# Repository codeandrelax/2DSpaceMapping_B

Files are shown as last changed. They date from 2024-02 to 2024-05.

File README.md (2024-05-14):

# AUTONOMNO VOZILO - PROJEKTNI ZADATAK
Ovaj repozitorijum sadži dokumentaciju potrebnu za izradu projektnog zadataka iz predmeta Računarska elektronika/Mikrokontrolerski sistemi na Elektrotehničkom fakultetu u Banjoj Luci. Na projekatu rade tri studenta na četvrtoj godini. Cilj projekta jeste implementacija sistema za autonomnu vožnju koji može bezbijedno i efikasno upravljati vozilom. Sistem se nadograđuje na [Joy-car](https://joy-it.net/en/products/mb-joy-car) sa specificiranim zahtjevima.

# Specifikacija projektnog zadataka 
### Upravljačka PCB ploča
Potrebno je realizovati PCB pločicu koja ispunjava sljedeće zahtjeve: 
* PCB pločica može biti maksimalno dvoslojna.
* Koristi se SMD tip komponenti
* Minimalna širina veze prilikom rutiranja iznosi 0.254 mm, a minimalno rastojanje između komponenata 0.1 mm.
* Korišćenje mikrokontrolera (MCU) tipa PIC24FJ64GAxx za upravljanje i kontrolu sistema.
* Podrška za komunikaciju putem UART, SPI i I2C interfejsa za povezivanje različitih komponenti.
* Integracija Wi-Fi modula za bežičnu komunikaciju i daljinsko upravljanje.
* Upotreba već postojećeg baterijskog napajanja.
* Budzet za kupovinu komponenata od 20 do 30 dolara.

### IR Distance Click senzor
* Kretanje vozila na osnovu očitavanja senzora
* Implementacija 2D mapiranja prostora oko vozila na osnovu očivatanja senzora.

## Aplikacija
* Razvoj aplikacije za prikazivanje okoline oko vozila.
* Mogućnost pokretanja i zaustavljanja vozila putem aplikacije, 2D prikaz reljefa.
   
## Projektovanje štampane ploče
* Šema 
kompletna_sema

* Layout  
  
  back_cu
  

* 3D model
  3d_model
 3d_model2

## Realizacija algoritma kretanja vozila

Potpuno integrisano samoupravljajuće vozilo Joy Car funkcioniše na taj način da se IR click senzor vozila najprije centrira tako da skenira prostor ispred sebe i vozilo se počinje kretati ravno, to je jedan od pet mogućih pravaca kretanja vozila. Nakon što vozilo prilikom kretanja naiđe na prepreku koja se nalazi na udaljenosti od 15cm, zaustavlja se i skenira se prostor oko vozila, tako što se okreće IR Distance Click senzor koji je postavljen na servo motoru koji se okreće za ugao od 45 stepeni u desnu stranu, odnosno lijevu. Nakon što na osnovu vrijednosti napona koju senzor generiše odredimo u kojem smjeru se prepreka nalazi najdalje, vozilo se počinje kretati u tom pravcu. Ukoliko su vrijednosti očitavanja senzora veće, tada se prepreka nalazi bliže vozilu i obratno. U slučaju da se prepreka nalazi jako blizu tada autić zbog širine točkova nije u mogućnosti da nesmetano skrene u željenom pravcu pa postoji i dodatni smijer kretanja, unazad. Tada autić najprije vozi nekoliko centimetara unazad, a zatim skrene u pravcu za koji je utvrdio da je najpovoljniji.  

Na slici ispod je prikazan primjer simulacije kretanja autića u lavirintu. 

  
  
Na gifu ispod prikazano je kretanje autića kroz lavirint:

gif

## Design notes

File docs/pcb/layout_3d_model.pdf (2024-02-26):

Projektni zadatak iz predmeta Mikrokontrolerski sistemi/Računarska elektronika

1

### Elektrotehnički fakultet Univerzitet u Banjoj Luci

## DOKUMENTACIJA PROJEKTNOG ZADATKA

## iz predmeta

## MIKROKONTROLERSKI SISTEMI/RAČUNARSKA ELEKTRONIKA

Student: | Mentori:
Tripić, Nemanja | prof. dr Željko Ivanović
Legenović, Dajana | dipl. inž Damjan Prerad
Savković, Božana

Projektni zadatak iz predmeta Digitalna obrada signala - izvještaj

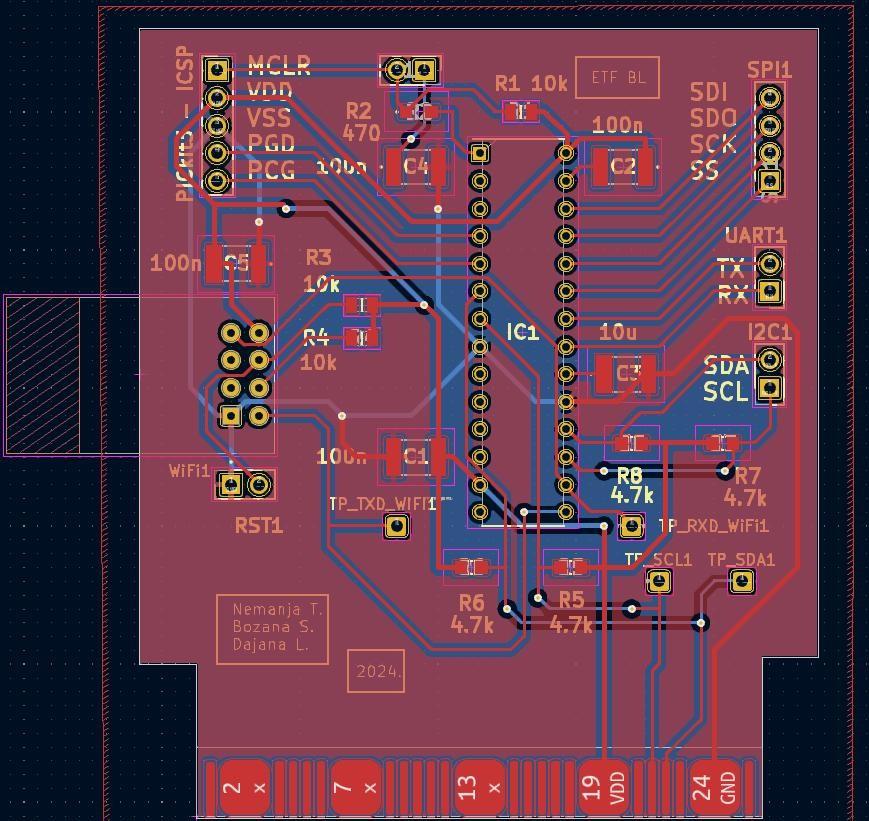
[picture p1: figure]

2

## RUTIRANJE KOMPONENATA

## Rutiranje komponenata

Nakon projektovanja šeme, potrebno je odraditi PCB layuot, rutirati komponente. Korišeno je dvoslojno rutiranje. Debljine linija za povezivanje su 0.254mm, a za napajanje 0.5mm. Minimalno rastojanje između komponenata je 0.1mm.

## Layout

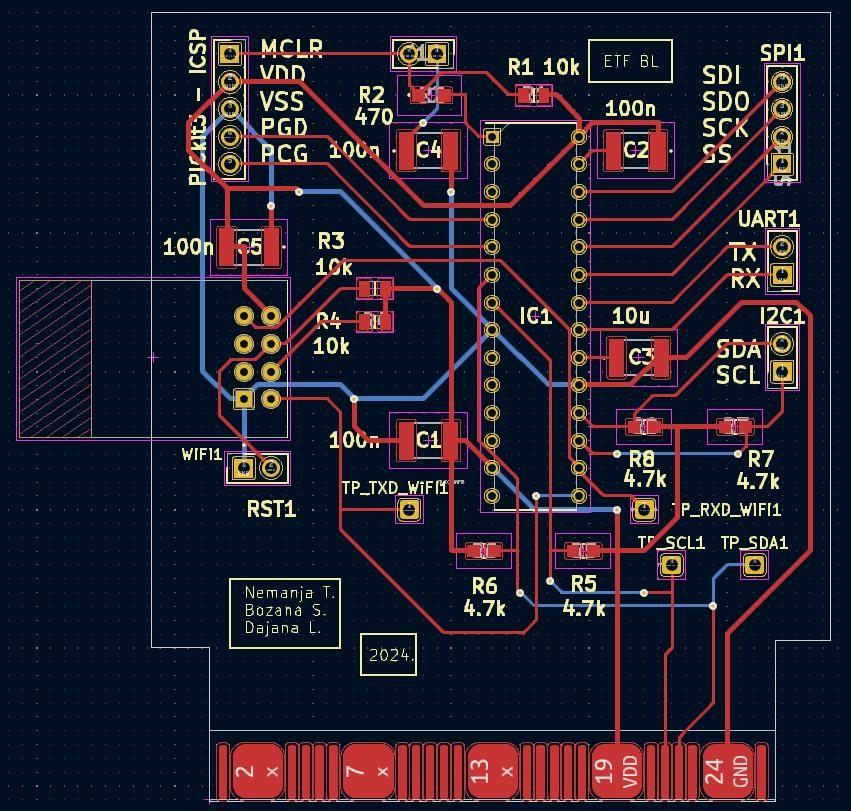
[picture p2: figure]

3

Prednja strana:

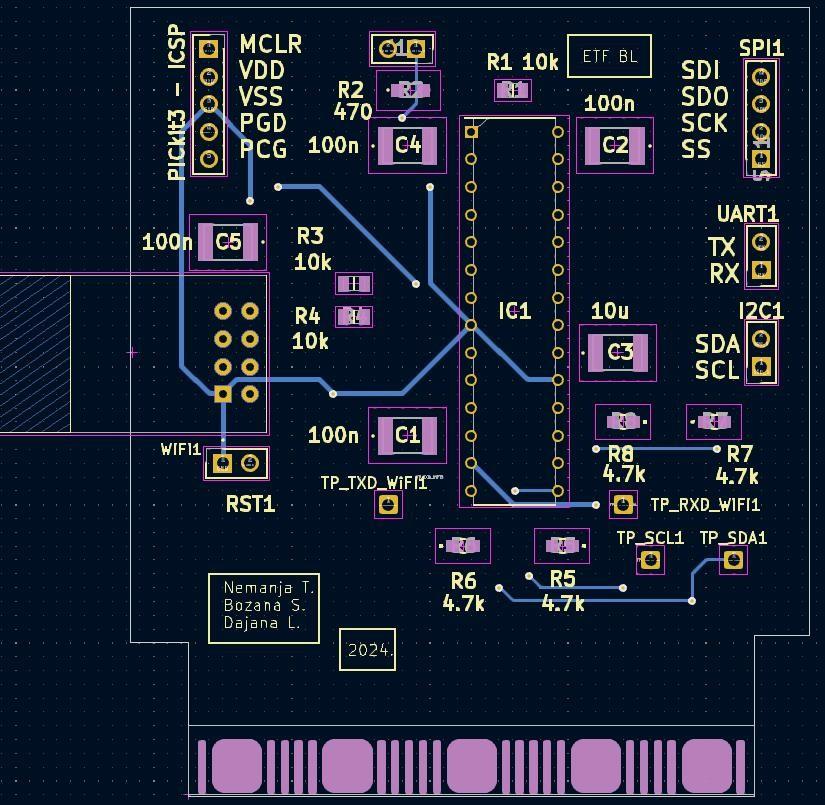
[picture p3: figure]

4

Zadnja strana:

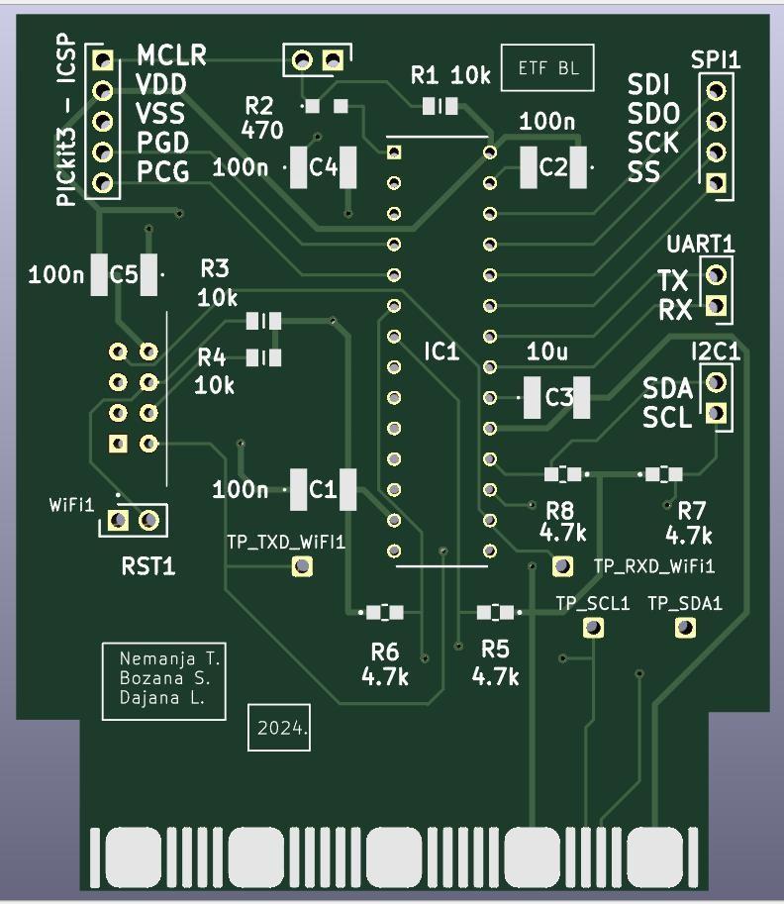
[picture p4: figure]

5

## 3D MODEL

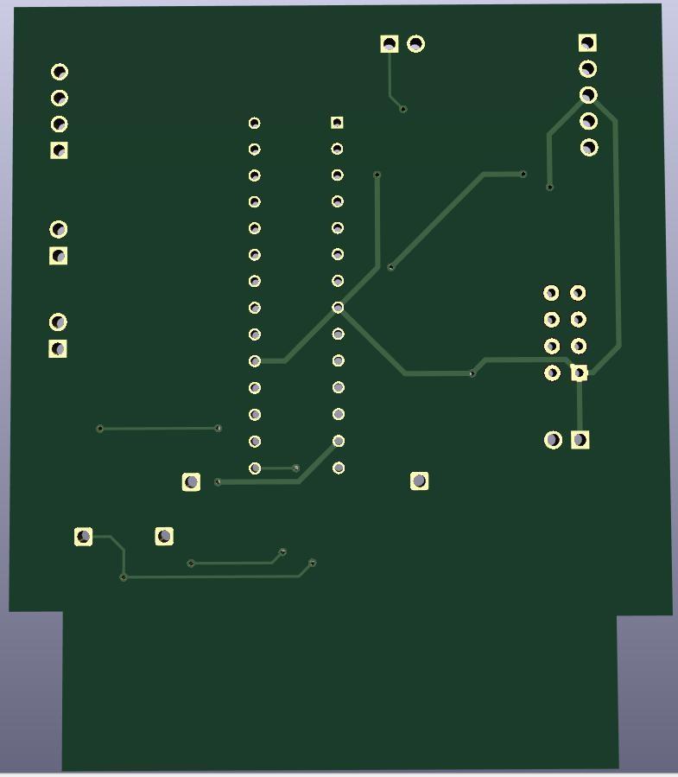
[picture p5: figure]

6

7

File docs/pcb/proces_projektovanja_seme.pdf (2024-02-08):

Projektni zadatak iz predmeta Mikrokontrolerski sistemi/Računarska elektronika

1

### Elektrotehnički fakultet Univerzitet u Banjoj Luci

## DOKUMENTACIJA PROJEKTNOG ZADATKA

## iz predmeta

## MIKROKONTROLERSKI SISTEMI/RAČUNARSKA ELEKTRONIKA

Student: | Mentori:
Tripić, Nemanja | prof. dr Željko Ivanović
Legenović, Dajana | dipl. inž Damjan Prerad
Savković, Božana

Projektni zadatak iz predmeta Digitalna obrada signala - izvještaj

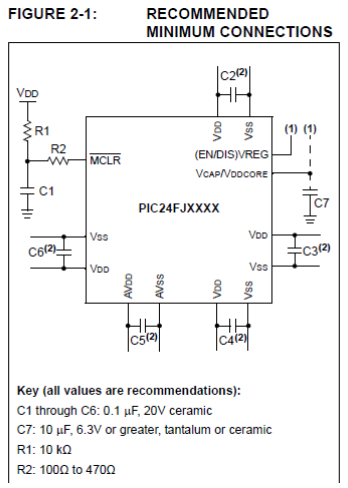
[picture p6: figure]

2

## PROJEKTOVANJE ŠEME

Kao što je već rečeno na wiki stranici stranici Planiranje projektovanja šeme, postoji nekoliko faza projektovanja. Prva faza je izbor mikrokontrolera koji zadovoljava specifikacije i dalje projektovanje ide u zavisnosti od njega. Izabran je mikrokontroler PIC24FJG4GA002 i njegov datasheet je na linku https://ww1.microchip.com/downloads/aemDocuments/documents/OTH/ProductDocuments/DataSheets/39881e.pdf. (https://ww1.microchip.com/downloads/aemDocuments/documents/OTH/ProductDocuments/DataSheets/39881e.pdf)

## 1. Dodavanje mikrokontrolera i osnovne šeme

U datasheet-u se može naći preporučena osnovna šema ukoliko se izabere dati mikrokontroler. Ona izgleda ovako:

Slika 1 – Minimalna šema

Dakle neophodno je koristiti sprežne kondenzatore između pinove VDD i VSS vrijednosti 0.1uF. Što se tiče šeme to je za sada sve što nam je bitno, ali za kasnije projektovanje biće bitno referencirati se na datasheet da bi se izabrao pravi tip kondenzatora, kao i minimalna daljina postavljanja pinova u odnosu na pinove mikrokontrolera.

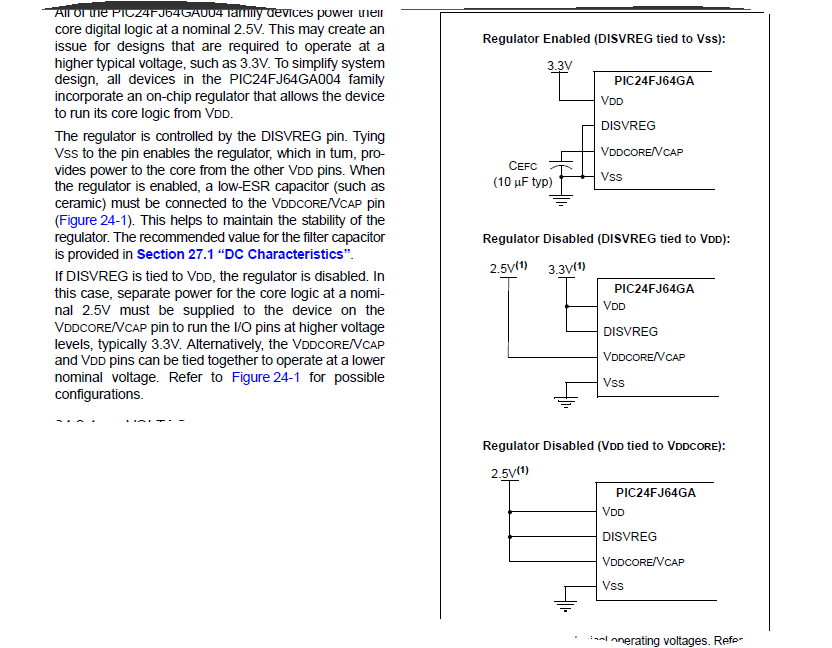
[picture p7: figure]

3

Dalje imamo dva otpornika jedan vrijednosti 10kΩ i drugi od 100Ω do 470Ω, te kondenzator od 0.1uF povezani na MCLR pin i na odgovarajući način na napajanje i na masu. MCLR pin ima dvije funkcije, koristi se pri programiranju i pri resetovanju mikrokontrolera. Detaljnije o tome kada budemo govorili o [dodavanju bloka za programiranje na šemu](#dodavanje-bloka-za-programiranje-na-šemu).

Ono što je još ostalo za kao dio osnovne konfiguracije šeme jeste spajanje pinova DISVREG (u slučaju našeg mikrokontrolera), te pina VCAP/VDDCORE. Ovi pinovi služe za omogućenje odnosno onemogućenje naponskog regulatora. Ukoliko želimo da naponski regulator bude omogućen potrebno je DISVREG spojiti na GND, a u tom slučaju VCAP/VDDCORE se spaja preko low-ESR(<5Ω) keramičkog kondenzatora od 10uF na GND.

Ako želimo da onemogućimo regulator spajamo DISVREG na VDD, a u tom slučaju je na VCAP/VDDCORE potrebno dovesti posebno napajanje sa nominalnih 2.5V. Opciono u ovom slučaju, moguće je i DISVREG i VCAP/VDDCORE spojiti na isti nominalni napon od 2.5V. Vidi datasheet (strana 215).

Slika ispod:

Slika 2 – Šema spajanja DISVREG i VCAP/VDDCORE

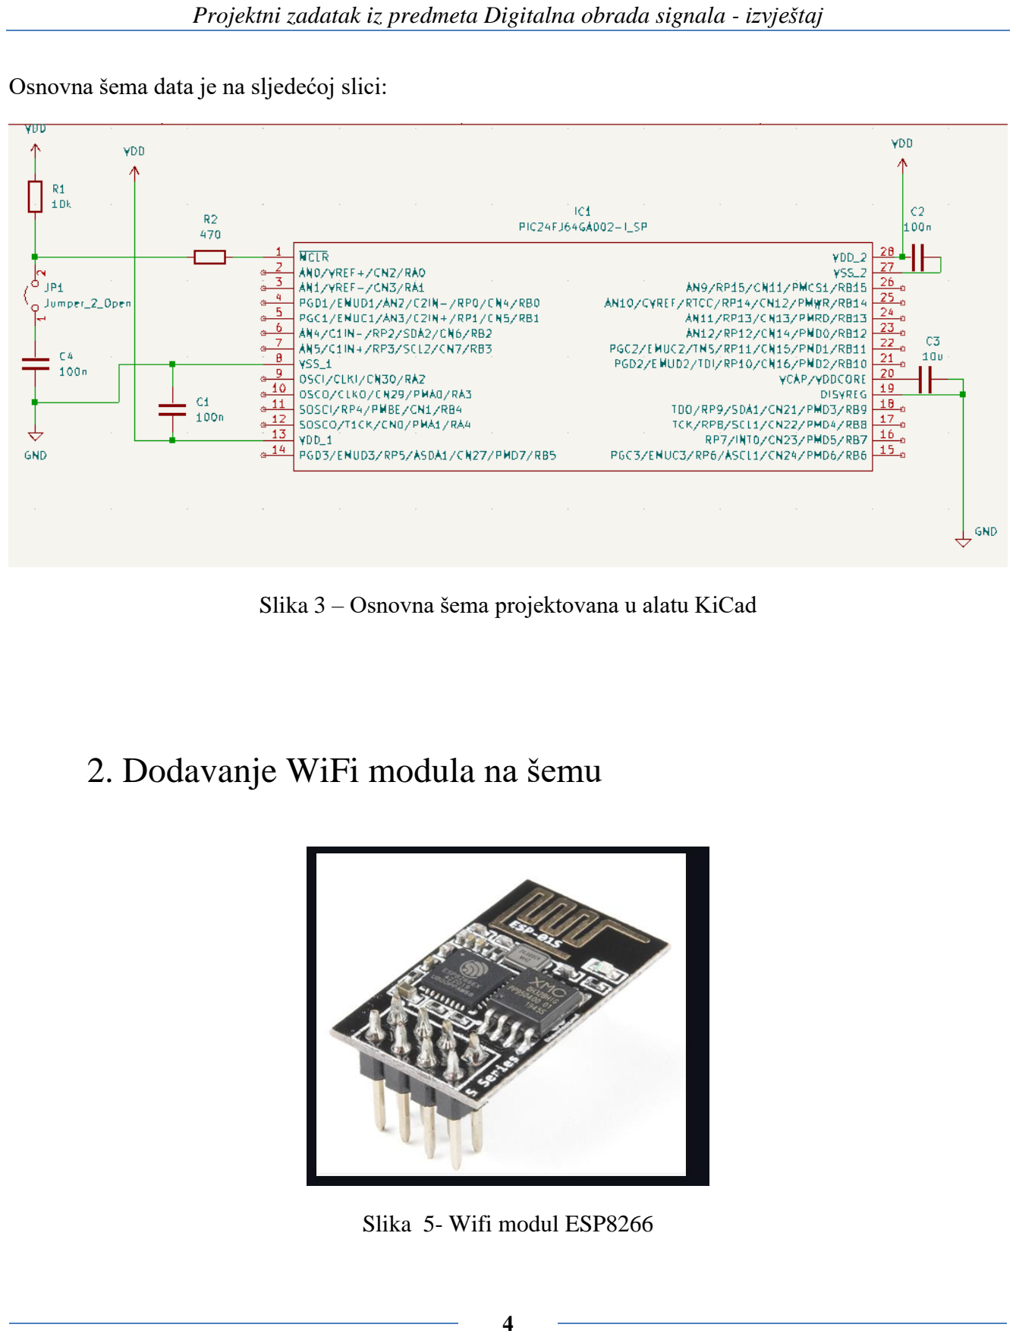
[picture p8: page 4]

4

Osnovna šema data je na sljedećoj slici:

Slika 3 – Osnovna šema projektovana u alatu KiCad

## 2. Dodavanje WiFi modula na šemu

Slika 5- Wifi modul ESP8266

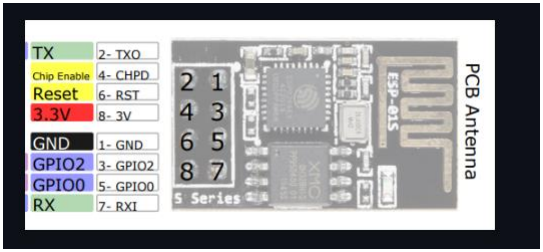
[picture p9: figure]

5

Za uspostavljanje wiFi komunikacije potrebno je koristiti wiFi modul WRL-17146, prikazan na slici iznad. Osnovna komponenta ovog modula je mikrokontroler ESP8266.

Neke od osnovnih osobina ovog modula su:

- L106 32-bitni mikrokontroler sa radnim taktom od 80 MHz.
- Ugradjena radna memorija, 64 KB instrukcijskog RAM-a i 96 KB RAM-a za podatke, te je podržano i do 4 MB eksterne fleš memorije.
- Podržava 802.11 b/g/n standarde bežične komunikacije
- Radna voltaža modula je obično izmedju 3.3V i 3.6V, što ga čini kompatibilnim sa većinom mikrokontrolera.
- Podržava I2C, SPI, UART, PWM i druge komunikacijske protokole.
- Niz GPIO pinova koji omogućavaju povezivanje sa drugim senzorima, aktuatorima itd.
- Optimizovan za nisku potrošnju energije, čime se olakšava rad sa baterijama i uredjajima sa ograničenim izvorima energije.

Pinovi za povezivanje WRL-17146

Slika 6 – pinovi wifi modula

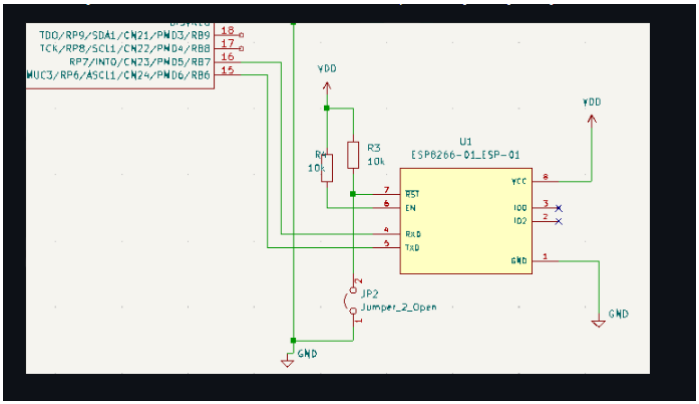
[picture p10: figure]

6

1.GND - pin za uzemljenje

2.TXO - linija za slanje podataka pomoću UART-a

3.GPIO2 - pin opšte namjene, broj 2

4.CHPD - linija za omogućenje/onemogućenje modula

5.GPIO1 - pin opšte namjene, broj 1

6.RST - linija za resetovanje modula

7.RX0 - linija za primanje podataka pomoću UART-a

8.VCC - linija za napanje, obično od 3.3V

Povezivanje modula WRL-17146 sa mikrokontrolerom

Povezivanje wiFi modula WRL-17146 sa mikrokontrolerom prikazano je na sljedećoj slici.

Slika 7 – šema nakon dodavanja wifi modula

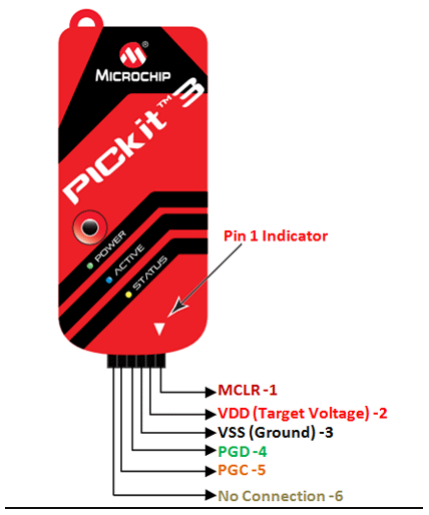
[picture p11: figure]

7

## 3. Dodavanje bloka za programiranje na šemu

Blok za programiranje podrazumijeva postavljanje odgovarajućih konektora na šemu predviđenih za programiranje mikrokontrolera. Za programiranje ćemo koristiti alat pod nazivom PICkit3. Njegov izgled je dat na sljedećoj slici:

Slika 4 – PICkit3

Kao što se vidi sa slike za korištenje ovog alata neophodno je obezbijediti konektore za 5 pinova. MCLR pin je pin 1 kontrolera, a i na PICkit3 je označen sa 1. Pošto se MCLR pin može koristiti i za programiranje i za resetovanje, u slučaju kada ga koristimo za programiranje potrebno je odvojiti kondenzator C1 od ostatka šeme i za to se koristi jumper, kao što smo već vidjeli na šemi sa slike 3. Sljedeća dva pina su napajanje i masa i njih spajamo standardno na Vdd odnosno na GND.

Nakon toga slijede pinovi 4 PGD i 5 PGC. To su pinovi koji koristeći ICSP protokol služe konkretno za samo programiranje. Ono o čemu treba voditi računa jeste da konektori za ove pinove budu što bliže odgovarajućim pinovima mikrokontrolera. U datasheet-u se još navodi da pul-ap otpornici, diode u serijskoj vezi i kondenzatori nisu prepopučeni, jer mogu da ometaju komunikaciju između mikrokontrolera i uređaja.

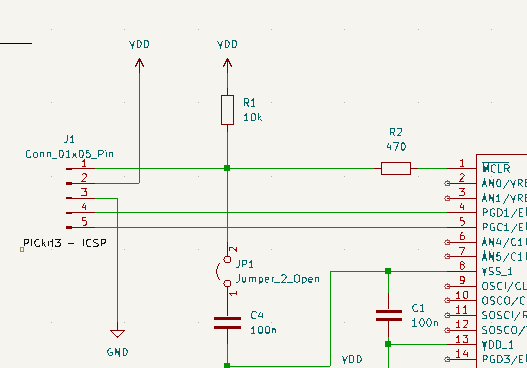
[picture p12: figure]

8

Šema nakon dodavanja konektora za PICkit3 i povezivanja sa mikrokontrolerom izgleda kao na slici:

Slika 5 – Dodavanja bloka za programiranje

## 4. Dodavanje bloka za napajanje

Blok za napajanje za sada nećemo projektovati, već ćemo koristiti napajanje od 3.3V koje možemo povezati preko već postojeće pločice iz joy-it kita. Za komunikaciju sa tom pločicom projektovali smo edge connector, pa u suštini napajanje dobijamo preko edge connector-a. Napajanje od 3.3V zadovoljava potrebe našeg mikrokontrolera, kao i wifi modula, te PICkit3 alata koji ćemo koristiti za programiranje.

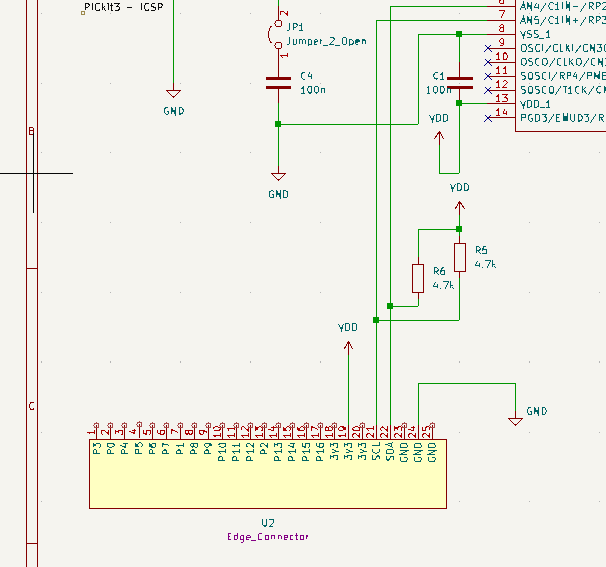
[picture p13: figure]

9

## 5. Dodavanje edge connector-a

Edge connector smo projektovali da bismo mogli komunicirati direktno sa već postojećom pločicom na vozilu. Više informacija o samom edge connetor može se naći na našoj wiki stranici Projektovanje otiska i footrprint-a za edge connector. Kao što smo rekli u poglavlju 4, napajanje ćemo uzimati sa postojeće pločice preko edge connector-a. To se može vidjeti sa sljedeće slike, gdje smo ažurirali šemu dodavanjame edge connector-a:

Slika 6 – Dodavanje edge connector-a na šemu

Osim samog napajanja, edge connector nam je bitna za komunikaciju preko I2C protokola, kojim ćemo upravljati kretanjem vozila. Na vozilu postoje dva točka sa motorima, koji se direktno upravljaju I2C protokolom, kao što je objašnjeno na wiki stranici Izučavanje dobijene štampane pločice.

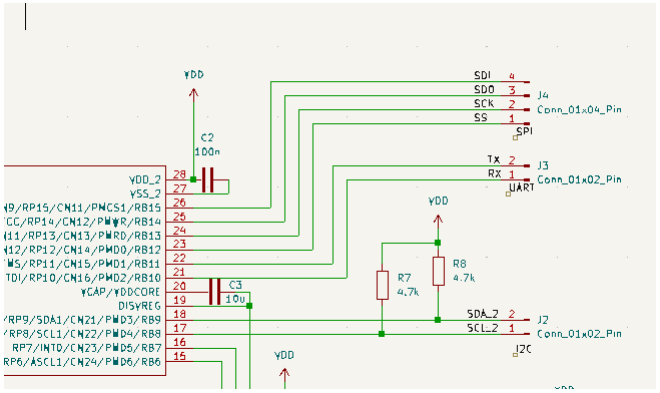
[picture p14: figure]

10

## 6. Dodavanje interfejsa za eksternu komunikaciju na šemu

Dodavanje interfejsa za eksternu komunikaciju prikazano je na slici na slici ispod.

Slika 7 – Konektori interfejsa za eksternu komunikaciju

Od interfejsa za komunikaciju spoljnim komponentama koristićemo SPI, UART i I2C komunikacione interfejse.

SPI

SPI (Serial Peripheral Interface) je serijski komunikacioni interfejs koji se često koristi za povezivanje mikrokontrolera sa perifernim uređajima, kao što su senzori, ekranu, memorijski čipovi itd. Ovaj interfejs je široko korišćen zbog svoje jednostavnosti i brzine.

SPI ima četiri linije za komunikaciju, a to su:

1. SDI(Serial Data In) - serijska linija za primanje podataka koja je povezana na pin broj 26 mikrokontrolera.
2. SDO(Serial Data Out) - serijska linija za slanje podataka koja je povezana na pin broj 25 mikrokontrolera.

11

3. SCK(Serial Clock) - takt impuls koji je povezan na pin 24 mikrokontrolera.
4. SS(Slave Select) - signal za selektovanje slave uredjaja (ukoliko ih ima više), koji je povezan na pin 23 mikrokontrolera.

UART

UART (Universal Asynchronous Receiver/Transmitter) je komunikacioni interfejs koji omogućava serijsku asinhronu komunikaciju između uređaja. Asinhrona komunikacija znači da podaci nisu sinhronizovani pomoću zajedničkog clock signala, već se koriste start i stop biti kako bi označili početak i kraj svakog bajta podataka.Za komunikaciju se koriste dvije fizičke linije:

1. TX(Transmit) - linija za slanje podataka koja se sa mikrokontrolerom povezuje pomoću pina broj 22.
2. RX(Receive) - linija za primanje podataka koja se sa mikrokontrolerom povezuje pomoću pina broj 21.

I2C

I2C (Inter-Integrated Circuit) je serijski komunikacioni interfejs koji omogućava sinhronu serijsku komunikaciju između više uređaja koristeći minimalan broj žica. Koristi dvije linije za komunikaciju:

1. SDA(Serial Data Line) - linija za prevos podataka koja je povezana na pin broj 18 mikrokontrolera.
2. SCL(Serial Clock) - linija za prenos takta koja je povezana na pin broj 17 mikrokontrolera.

Da bi komunikacija bila ispravna potrebno je na svaku od linija za komunikaciju dodati i pull up otpornik od 4.7kOhm.

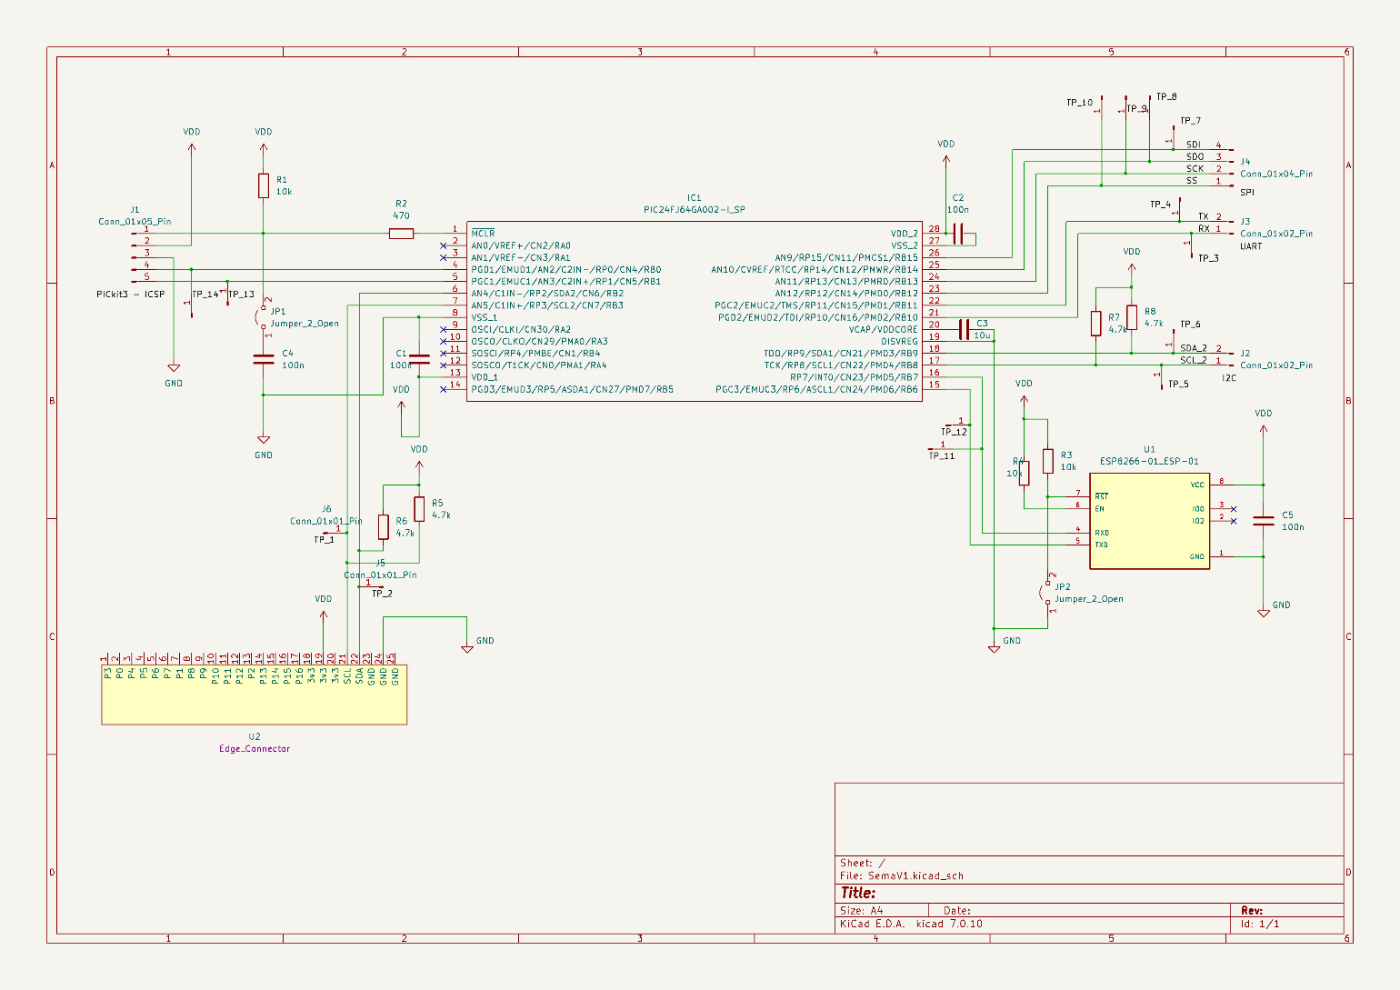
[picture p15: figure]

12

## 7. Kompletna šema

Na kraju kompletna šema izgleda kao na slici:

13

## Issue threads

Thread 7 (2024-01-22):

Projektovanje otiska (footprint) i simbola za edge connector

nemanjatr, 2024-01-22:
- Cilj ovog zadatka jeste da se isprojektuje simbol u KiCad alatu koji će se koristiti na električnoj šemi, kao i footprint koji odgovara kreiranom simbolu i specifikacijama edge connector-a koji projektujemo.
- Rezultat zadatka je model edge connector-a koji ćemo koristiti u daljem projektovanju ploče, a koji nam je neophodan za komunikaciju sa postojećom pločom na vozilu.
- Osim toga rezultat zadatka je wiki stranica sa opisom i izgledom isprojektovanog edge connector-a.
- Vremenska procjena: 10 sati

nemanjatr, 2024-01-30:
Utrošeno vrijeme: 12 sati
Težina zadatka: 7 (10)

Closed 2024-03-25.

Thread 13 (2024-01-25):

Izvođenje interfejsa sa eksternu I2C, SPI, UART komunikaciju

nemanjatr, 2024-01-25:
- U skladu sa specifikacijom zadatka potrebno je izvesti I2C, SPI i UART konektore sa mikrokontrolera
- Ažurirati izgled šeme na wiki stranici tako da sadrži ove konektore
- Vremenska procjena: 2 sata

dleg98, 2024-02-07:
Utroseno vrijeme : 2h
Težina zadatka: 5

Closed 2024-03-25.

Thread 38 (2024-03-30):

Testiranje IR Distance Click komponente

nemanjatr, 2024-03-30:
- Potrebno je upoznati sa komponentom, njenim načinom rada i povezivanjem.
- A zatim i testirati njen rad jednostavnim programom kojim se simulira približavanje prepreke senzoru, koji uključuje LED diodu.
- Rezultat rada je wiki stranica sa objašnjenjem komponente i njenim testiranjem.
- Potrebno vrijeme: 5 sati

nemanjatr, 2024-03-30:
- Dodan fajl na repozitorijum sa C kodom za testiranje rada senzora (firmware/testing/sensor.c)
- Dodana wiki stranica sa objašnjenjem procesa testiranja senzora (Wiki/ 04 - Testiranje i uklapanje pojedinačnih komponenata/ Testiranje IR Distance Click komponente)
- Utrošeno vrijeme: 6 sati
- Težina zadatka: 4 (10)

Closed 2024-04-22.

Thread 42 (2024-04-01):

Testiranje pokretanja servo motora za senzor

nemanjatr, 2024-04-01:
- Potrebno je iskoristiti jedan PWM modul mikrokontrolera za generisanje signala koji će pokretati servo motor na kojem je pričvršćen senzor za mjerenje udaljenosti.
- Istražiti način korištenja PWM-a za pokretanje konktretnog servo motora.
- Rezultat rada je kod koji se spušta na mikrokontroler i izvršava pokretanje motora, te wiki stranica na kojoj je dokumentovan rad.
- Procjena vremena: 8 sati

Closed 2024-05-14.

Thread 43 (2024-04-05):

Konfiguracija I2C-a za pokretanje motora na točkovima

nemanjatr, 2024-04-05:
- Potrebno je konfigurisati I2C modul(i to modul broj 2 mikrokontrolera, pinovi 6 i 7) na mikrokontroleru tako komunicira sa joy-it pločom na kojoj postoji interno PWM modul koji generiše PWM signale za pokretanje točkova.
- Procjena vremena 10 sati
- Rezultat rada je kod za mikroC kompajler, koji se spušta na mikrokontroler, te dokumentacija rada na wiki stranicama.

nemanjatr, 2024-04-15:
- Težina zadatka: 10 (10)
    - Teško dostupna i nekompletna dokumentacija postojeće pločice otežala je izvršavanje ovog zadatka. Kao i neiskustvo rada sa   I2C interfejsom.
- Utrošeno vrijeme: 80 sati

Closed 2024-04-22.

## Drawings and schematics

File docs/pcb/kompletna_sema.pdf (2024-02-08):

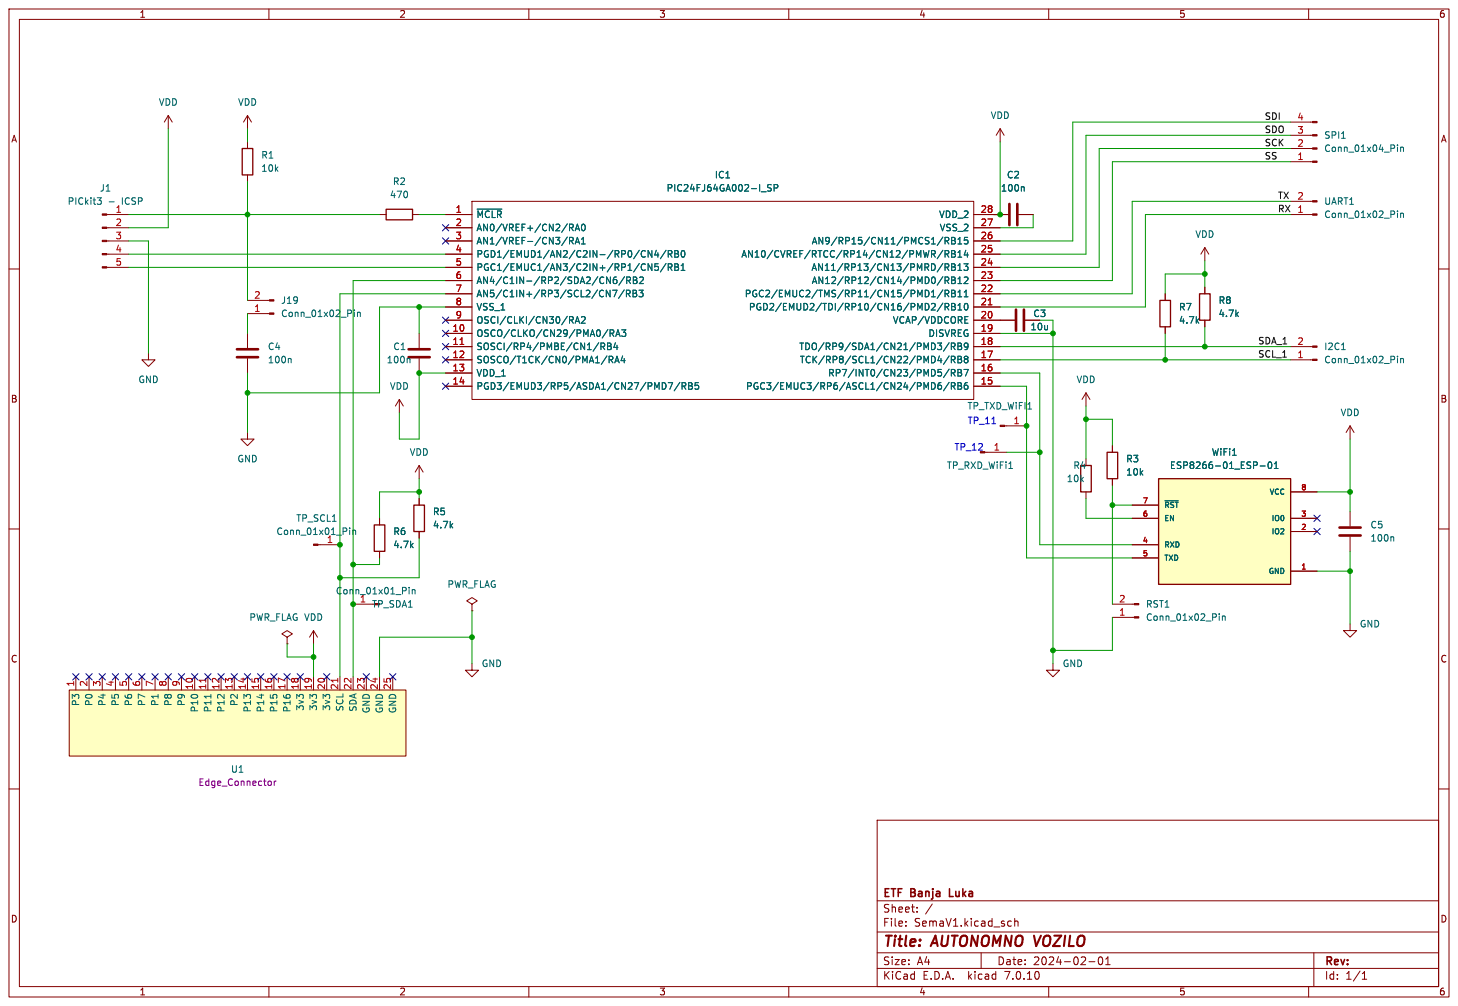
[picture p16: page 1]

2 3v3 20 SCL 21 SDA 22 GND 23 GND 24 GND 25 P4

Id: 1/1 Title: AUTONOMNO VOZILO

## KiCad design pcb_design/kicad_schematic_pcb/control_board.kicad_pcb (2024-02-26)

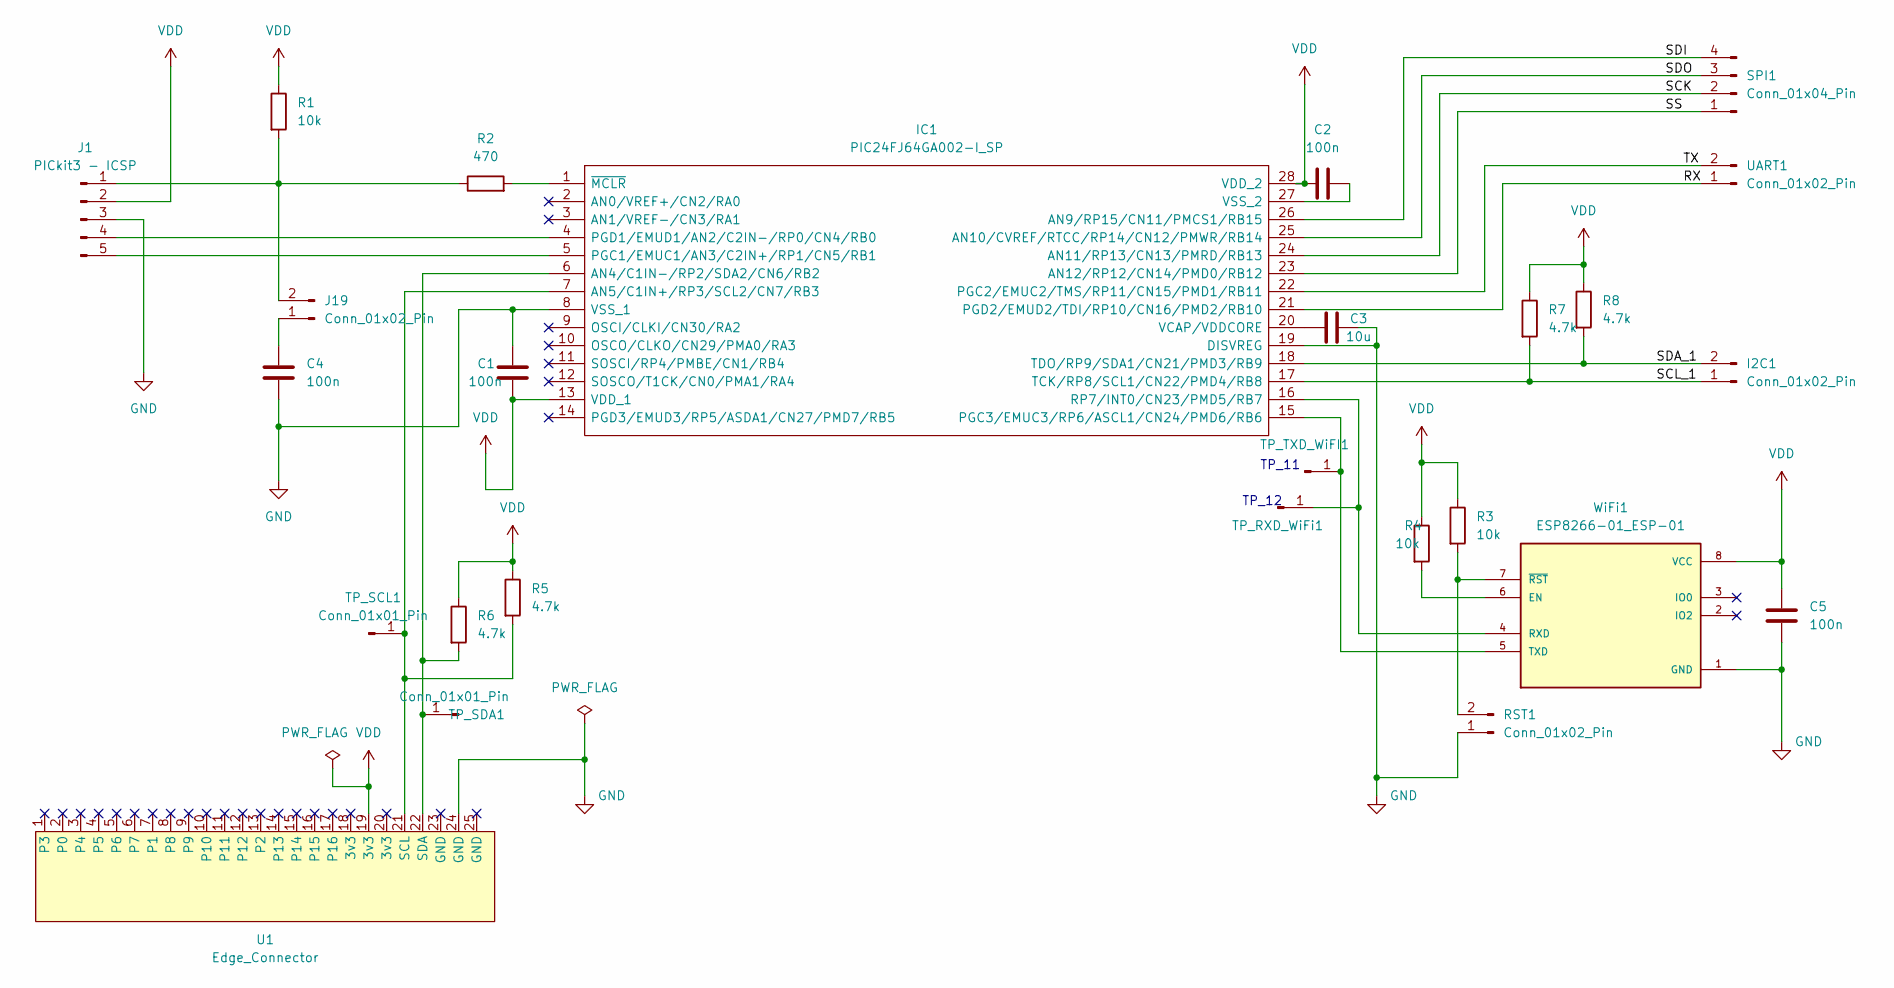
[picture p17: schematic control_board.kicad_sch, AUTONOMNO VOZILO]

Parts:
C1, C2, C4, C5: 100n; C1812
C3: 10u; C1812
I2C1: Conn_01x02_Pin; HDRV2W66P0X254_1X2_508X254X874P
IC1: PIC24FJ64GA002-I_SP; DIP794W56P254L3486H508Q28N; Mouser Part Number 579-PIC24FJ64GA002SP
J1: PICkit3 - ICSP; HDRV5W67P0X254_1X5_1229X234X821P
J19: Conn_01x02_Pin; HDRV2W66P0X254_1X2_508X254X874P
R1, R3, R4: 10k; RESC2012X65N
R2: 470; ERA6VK
R5, R6, R7, R8: 4.7k; ERA6AEB1020V
RST1: Conn_01x02_Pin; HDRV2W66P0X254_1X2_508X254X874P
SPI1: Conn_01x04_Pin; HDRV4W64P0X254_1X4_1016X254X889P
TP_RXD_WiFi1: Conn_01x01_Pin; SolderWire-0.1sqmm_1x01_D0.4mm_OD1mm
TP_SCL1: Conn_01x01_Pin; SolderWire-0.1sqmm_1x01_D0.4mm_OD1mm
TP_SDA1: Conn_01x01_Pin; SolderWire-0.1sqmm_1x01_D0.4mm_OD1mm
TP_TXD_WiFI1: Conn_01x01_Pin; SolderWire-0.1sqmm_1x01_D0.4mm_OD1mm
U1: Edge_Connector
UART1: Conn_01x02_Pin; HDRV2W66P0X254_1X2_508X254X874P
WiFi1: ESP8266-01_ESP-01; XCVR_ESP8266-01_ESP-01; PARTREV V1.2

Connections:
/RX: IC1.21 (PGD2/EMUD2/TDI/RP10/CN16/PMD2/RB10), UART1.1
/SCK: IC1.24 (AN11/RP13/CN13/PMRD/RB13), SPI1.2
/SCL_1: I2C1.1, IC1.17 (TCK/RP8/SCL1/CN22/PMD4/RB8), R7.2
/SDA_1: I2C1.2, IC1.18 (TDO/RP9/SDA1/CN21/PMD3/RB9), R8.2
/SDI: IC1.26 (AN9/RP15/CN11/PMCS1/RB15), SPI1.4
/SDO: IC1.25 (AN10/CVREF/RTCC/RP14/CN12/PMWR/RB14), SPI1.3
/SS: IC1.23 (AN12/RP12/CN14/PMD0/RB12), SPI1.1
/TX: IC1.22 (PGC2/EMUC2/TMS/RP11/CN15/PMD1/RB11), UART1.2
GND: C1.1, C3.2, C4.2, C5.1, IC1.8 (VSS_1), IC1.19 (DISVREG), J1.3, RST1.1, U1.24 (GND), WiFi1.1 (GND)
unnamed: IC1.6 (AN4/C1IN-/RP2/SDA2/CN6/RB2), R6.2, TP_SDA1.1, U1.22 (SDA)
unnamed: IC1.7 (AN5/C1IN+/RP3/SCL2/CN7/RB3), R5.2, TP_SCL1.1, U1.21 (SCL)
unnamed: IC1.5 (PGC1/EMUC1/AN3/C2IN+/RP1/CN5/RB1), J1.5
unnamed: IC1.15 (PGC3/EMUC3/RP6/ASCL1/CN24/PMD6/RB6), TP_TXD_WiFI1.1, WiFi1.5 (TXD)
unnamed: IC1.4 (PGD1/EMUD1/AN2/C2IN-/RP0/CN4/RB0), J1.4
unnamed: IC1.16 (RP7/INT0/CN23/PMD5/RB7), TP_RXD_WiFi1.1, WiFi1.4 (RXD)
unnamed: C3.1, IC1.20 (VCAP/VDDCORE)
unnamed: C2.2, IC1.27 (VSS_2)
unnamed: IC1.1 (~MCLR), R2.2
unnamed: J1.1, J19.2, R1.2, R2.1
unnamed: C4.1, J19.1
unnamed: R3.2, RST1.2, WiFi1.7 (~RST)
unnamed: R4.2, WiFi1.6 (EN)
VDD: C1.2, C2.1, C5.2, IC1.13 (VDD_1), IC1.28 (VDD_2), J1.2, R1.1, R3.1, R4.1, R5.1, R6.1, R7.1, R8.1, U1.19 (3v3), WiFi1.8 (VCC)

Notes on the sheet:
TP_12
TP_11

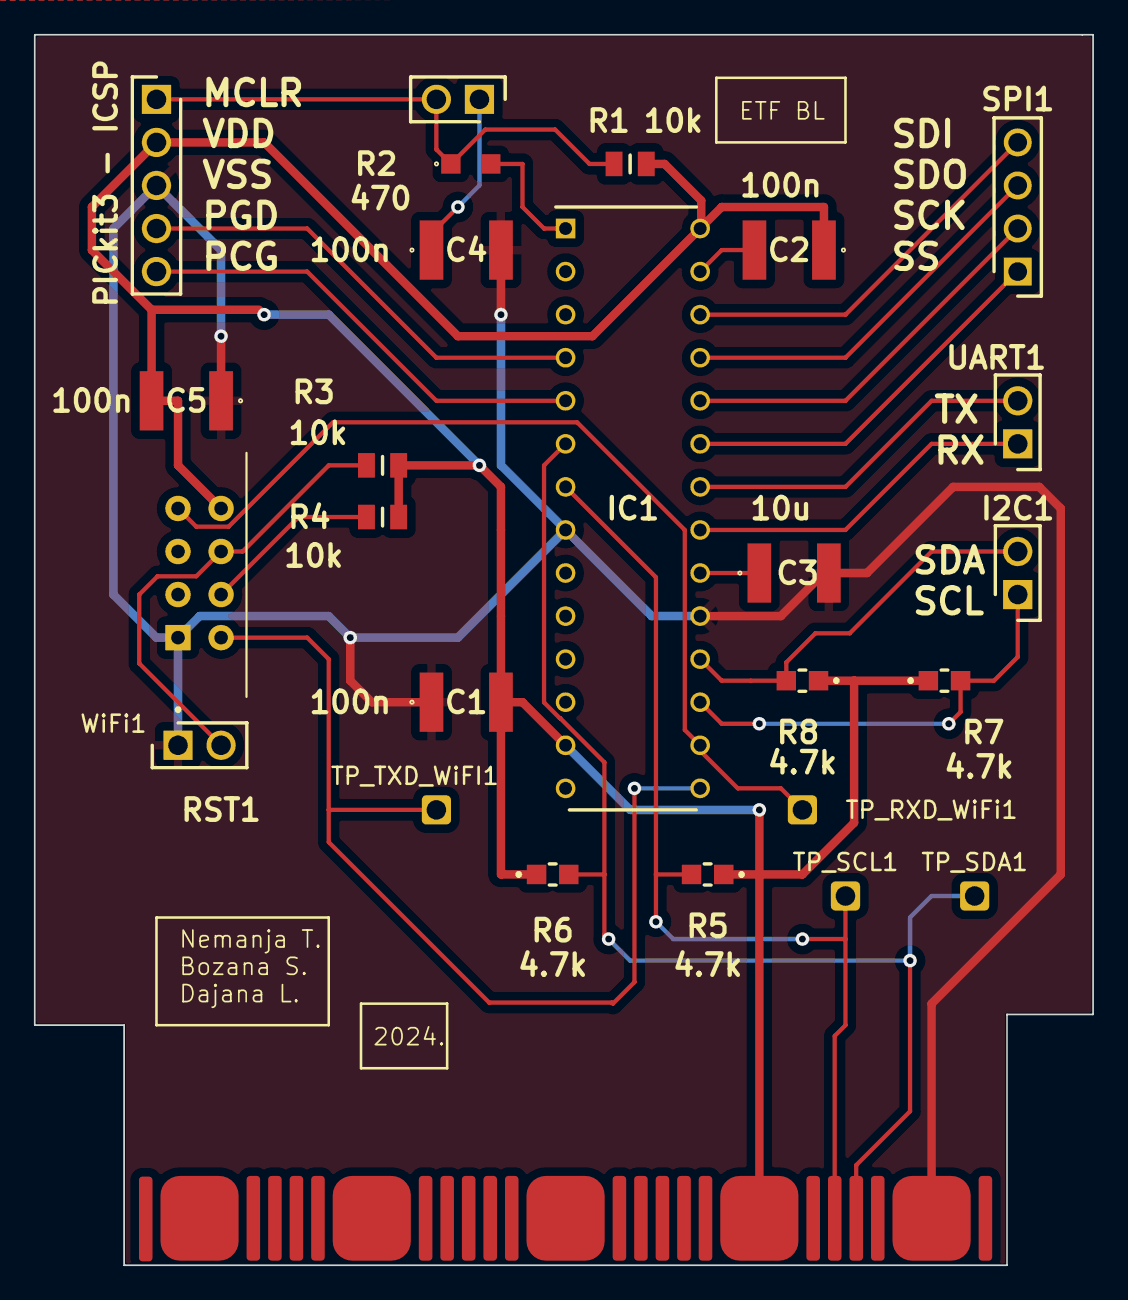
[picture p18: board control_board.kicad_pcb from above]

Board: 2 copper layers, 62.4 x 72.6 mm, 26 parts (0 on the bottom side), 23 nets.

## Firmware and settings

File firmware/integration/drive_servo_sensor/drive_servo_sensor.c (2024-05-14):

/**
 * @file drive_servo_sensor.c
 * @brief File with second stop of project integration.
 *
 * This file contains code that integrates driving the car module
 * with servo-sensor module. So this code does all the stuff that
 * is shown in integration/servo_sensor.c program, but also has the 
 * ability to drive the car around based on sensor reading.
 * Besides servo-sensor functions this code has:
 * - initialization of I2C for driving
 * - functions for driving forward, and braking the car
 * 
*/

/**
 * @name Macros used in program 
 * @{
*/
/** @brief Macro that defines speed of the vehicle (0-255) */ 
#define SPEED 125
/** @brief I2C address of the device */
#define DEVICE_ADDR 0xE0
/** @} */

/** @name Declaring duty cycles which will be used for servo_sensor scanning 
 * @{
*/
unsigned pwm_period = 0;
float    duty_cycle = 0;
float    duty_cycles[] = {2.0, 4.7, 7.5, 10.2, 13.0};
/** @} */

/**
 * @name Sensor reading values
 * @{
*/
unsigned sensor_reading = 0;
unsigned sensor_values[5] = {0};
/** @} */

/**
 * @name Enable Software I2C communication, through the desired pins
 * @{
 
*/
sbit Soft_I2C_Sda           at RB2_bit;
sbit Soft_I2C_Scl           at RB3_bit;
sbit Soft_I2C_Sda_Direction at TRISB2_bit;
sbit Soft_I2C_Scl_Direction at TRISB3_bit;
/** @} */

/**  
 * Function that initializes servo_sensor, by setting a PWM pin, and configures PWM.
*/
void initialize_servo_for_sensor()
{
    
    /** set pin RB14 to work in open drain configuration */
    ODCB.F14 = 1;   

    /** set up PWM pin, RB(P)14  */
    Unlock_IOLOCK();
    PPS_Mapping_NoLock(14, _OUTPUT, 18);     
    Lock_IOLOCK();

    /** get PWM period for duty cycle count */
    /** set 50Hz period, channel 1, no prescaler, timer 2 */
    pwm_period = PWM_Init(50, 1, 0, 2);  
    PWM_Start(1);
}


/**
 * Functions that sets servo to its starting position,
 * by setting appropriate duty cycle of the PWM
*/
void set_servo_sensor_to_starting_pos()
{
    duty_cycle = 7.5;
    PWM_Set_Duty(duty_cycle * pwm_period / 100, 1);
}



/**
 * Function that initializes ADC needed for sensor reading 
*/
void initialize_ADC()
{
	/** Init ADC to use 10-bit module, and use Internal voltage reference(AVDD, AVSS) */
    ADC1_Init_Advanced(_ADC_INTERNAL_REF);       
}




/**
 * Function for I2C controller configuration. 
 * It addresses device, then desired register, and puts some value in it
*/
void I2C_Send_Message(unsigned short dev_addr, unsigned short reg_addr, unsigned short data_value)
{
    Soft_I2C_Start();
    Soft_I2C_Write(dev_addr);
    Soft_I2C_Write(reg_addr);
    Soft_I2C_Write(data_value);
    Soft_I2C_Stop();
}


/**
 * Function for I2C controller ,on the driver board, initialization.
 * What is does is that is addresses some registers of the PCA9633 I2C driver
 * ,according to the datasheet, and puts appropriate values in them, in order for
 * the car to be able to drive. 
*/
void initialize_I2C()
{
	Soft_I2C_Init();
	Delay_ms(100);
	 /* Set MODE1 register of PCA9633
	  * AIx                   - Auto-Increment disabled
	  * SLEEP bit set to 0    - Normal Mode
	  * SUBx bit set to 0     - PCA does not respond to subadresses
	  * ALLCALL bit set to 1  - PCA9633 responds to ALLCALL address (0xE0)
	 */
	 I2C_Send_Message(DEVICE_ADDR, 0x00, 0x01);
	 /* Set LEDOUT register of PCA9633
	  * LEDx output state control - all set to 0x10 which results in 0xAA value put into LEDOUT register
	 */
	 I2C_Send_Message(DEVICE_ADDR, 0xE8, 0xAA);
}


/**
 * Function for driving the car forward by setting PWM values and thus
 * controlling the DC motors on the wheels.
*/
void drive_forward()
{
    /* Set PWMx (x = 0, 1, 2, 3) registers to values according to datasheet in order for vehice to go forward*/
    I2C_Send_Message(DEVICE_ADDR, 0x02, 0);
    I2C_Send_Message(DEVICE_ADDR, 0x03, SPEED);
    I2C_Send_Message(DEVICE_ADDR, 0x04, 0);
    I2C_Send_Message(DEVICE_ADDR, 0x05, SPEED);
}


/**
 * Function for braking the wheels of the car, that are
 * effectively stopping the car. 
*/
void brake()
{
    I2C_Send_Message(DEVICE_ADDR, 0x02, 0);
    I2C_Send_Message(DEVICE_ADDR, 0x03, 0);
    I2C_Send_Message(DEVICE_ADDR, 0x04, 0);
    I2C_Send_Message(DEVICE_ADDR, 0x05, 0);
}



/**
 * Function that moves servo_sensor 180 degrees and stores sensor reading from different positions 
 * Moving the servo is done in for loop, by changing PWM duty cycles with some delay because
 * of the limits of servo motor. 
*/
void scan_space_with_sensor()
{
    unsigned i = 0;
    /* Clear the old sensor values */
    for(i=0; i < 5; i++)
    {
       sensor_values[i] = 0;
    }

	/* Move the servo around with PWM, and take sensor readings */
    for(i = 0; i<5; i++) 
    {
    	duty_cycle = duty_cycles[i];
      	PWM_Set_Duty(duty_cycle * pwm_period / 100, 1);
      	sensor_values[i] = ADC1_Get_Sample(9);
      	Delay_ms(600);

    }

     /* always return sensor to face front */
     set_servo_sensor_to_starting_pos();
     Delay_ms(600);
}


/**
 * Main function, entry point of the program
*/
void main()
{

	unsigned i = 0;

	AD1PCFG = 0xFDFF;        // set all pins to digital except pin AN9(RB15)
	LATB = 0;
	TRISB = 0;
	TRISB.F15 = 1;          // set pin AN9(RB15) as input

	/* Initialization of the needed components */
	initialize_I2C();
	Delay_ms(100);
	initialize_ADC();
	Delay_ms(100);
	initialize_servo_for_sensor();
	Delay_ms(100);

	/* Set servo to defaul position that is to face front */
	set_servo_sensor_to_starting_pos();
	Delay_ms(600);


	drive_forward();

	while(1)
	{
		/* 
		 * The car drives forward, and servo_sensor stays in its initial position 
		 * until obtacle within predefined stop range of 300 is observed 
		 * ,after that the car stop and  servo_sensor scans the space around it*/
		sensor_reading = ADC1_Get_Sample(9);
		if(sensor_reading >= 300){
			brake();
		   	scan_space_with_sensor();
		}
	}
}

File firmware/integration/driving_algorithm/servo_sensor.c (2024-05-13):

/**
 * @file servo_sensor.c
 * @brief File containing function definitions for servo_sensor module.
 * This file contains function definitions of functions that are used
 * for controlling the servo_sensor component of the vehicle, and also some
 * variables needed in that process. There are functions for for initializing
 * servo_sensor, that is setting PWM pins, and values on that pins, and alse
 * setting appropriate pin to analog for taking the input from sensor and 
 * AD convertor. Also there is function for scanning the space with sensor.
 * This implies setting servo in several positions and taking the value of
 * the IR Distance sensor attached to servo in that position, and saving it 
 * in some variables.
*/

#include "servo_sensor.h"

/** Number of servo-sensor positions, that is how many different PWMs are */
#define SENSOR_POSITIONS 10
/** Number of servo-sensor front positions*/
#define FRONT_POSITIONS 3

/**
 * @name PWM variables
 * Variables for setting PWM to different values, and thus controll servo-sensor
 * @{
*/
unsigned pwm_period = 0;
float    duty_cycle = 0;
float    duty_cycles[] = {2.0, 2.9, 4.9, 5.8, 7.9, 8.8, 10.5, 11.4, 12.1, 13.5};
float    front_duty_cycles[] = {6.0, 7.5, 9.0};
/** @} */


/** Array that store sensor values in each position of the sensor*/
unsigned sensor_values[SENSOR_POSITIONS] = {0};

/** Array that store sensor values after processing, each values in this array 
    is associated with one driving direction */
unsigned sensor_values_processed[DIRECTIONS] = {0};

/** Values to store 3 measurements in each sensor positions */
unsigned sensor_value_1, sensor_value_2, sensor_value_3 = 0;

/** Array that store sensor values in front positions of the servo_sensor */
unsigned front_reading[FRONT_POSITIONS] = {0};


/*
 * Function for initializing servo-sensor. First it initialies ADC 10-bit module, then sets pin
 * RB14 to work in open drain configuration, remapping pin RP14 to OUTPUT_COMPARE module.
 * Setting PWM to 50 Hz, channel 1, no prescaler, timer2, and then starting the PWM.
*/
void initialize_servo_sensor()
{	
	/* Init ADC to use 10-bit module, and use Internal voltage reference(AVDD, AVSS) */
	ADC1_Init_Advanced(_ADC_INTERNAL_REF); 
	/* Set pin RB14 to work in open drain configuration */
    ODCB.F14 = 1;   							
	/* Remapping pin RP14 to OUTPUT_COMPARE module for PWM*/
    RPOR7 = 0x0012;
	/* Set 50Hz period, channel 1, no prescaler, timer 2 */
    pwm_period = PWM_Init(50, 1, 0, 2);   
    PWM_Start(1);
}


/*
 * Function for setting servo-sensor to starting position
*/
void set_servo_sensor_to_starting_pos()
{
	/* starting position is for duty_cycle 7.5 */
	duty_cycle = 7.5;
    PWM_Set_Duty(duty_cycle * pwm_period / 100, 1);
}


/*
 * Function for scaning the space with servo-sensor
*/
void scan_space_with_sensor()
{
    unsigned i = 0;
    
    /* Clear old values in storing variables and arrays */
    sensor_value_1 = 0;
    sensor_value_2 = 0;
    sensor_value_3 = 0;
    
    for(i = 0; i < 3; i++)
    {
    	front_reading[i] = 0;
    }
   
    for(i = 0; i < 10; i++)
    {
       	sensor_values[i] = 0;
    }
    
    for(i = 0; i < 5; i++)
    {
       	sensor_values_processed[i] = 0;
    }
    
    /* Get sensor values, 3 measurements are taken in each position, and there average value is store into array */
    for(i = 0; i < SENSOR_POSITIONS; i++)
    {
		duty_cycle = duty_cycles[i];
		PWM_Set_Duty(duty_cycle * pwm_period / 100, 1);
		Delay_ms(50);

		sensor_value_1 = ADC1_Get_Sample(9);
		Delay_ms(35);
		sensor_value_2 = ADC1_Get_Sample(9);
		Delay_ms(35);
		sensor_value_3 = ADC1_Get_Sample(9);
		Delay_ms(35);

		sensor_values[i] = (sensor_value_1 + sensor_value_2 + sensor_value_3) / 3;
    }

	/* Filtering sensor readings from all sensor positions, into an array of values that length 
	   corresponds with number of directions vehicle can go */
    for(i = 0; i < DIRECTIONS; i++)
    {
        sensor_values_processed[i] += sensor_values[i * 2];
        sensor_values_processed[i] += sensor_values[i * 2] + 1;
    }
    
    Delay_ms(50);
    
    /* Get values of the sensor in fron positions  */
    for(i = 0; i < FRONT_POSITIONS; i++)
    {
        duty_cycle = front_duty_cycles[i];
        PWM_Set_Duty(duty_cycle * pwm_period / 100, 1);
        Delay_ms(200);
        front_reading[i] = ADC1_Get_Sample(9);
        Delay_ms(35);
    }

    /* Get servo-sensor back to starting position */
    set_servo_sensor_to_starting_pos();
    Delay_ms(75);
}

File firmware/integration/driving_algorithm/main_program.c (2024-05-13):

/**
 * @file main_program.c
 * @brief Main file of the program.
 
 * This file contains main function of the program that serves as an
 * entry point. It controls all the behavious of the complete program.
 * It initialies all the necesseary components of the system, and then
 * using the functions from other modueles, does all the work.
*/


#include "car_drive.h"
#include "servo_sensor.h"

/**
 * @brief Variable to store sensor value.
 *
 * Varible that saves the value of the sensor when the vehicle is going straight.
 */
unsigned sensor_reading = 0;

/**
 * @brief Array in which fron sensor values are store.
 *
 * Array that saves the values of the sensor when the vehicle 
 * stopped, scanned the space for further moving and is scanning
 * in front of itself for possible obstacle that is to close
 * 
 */
unsigned extern front_reading[];

/**
 * @brief Array in which sensor values are store.
 *
 * Array that saves the values of the sensor when the vehicle is stopped and is
 * scanning  space for further moving
 * 
 */
unsigned extern sensor_values_processed[];


/**
 * @brief Function that determines direction of the car after scaning the space.
 *
 * This function is called after vehicle encounters an obstacle, stops its
 * moving, and scans the space. Based on the values in sensor_values[] array
 * the vehicle determines which of the five directions possible it is going
 * to take.
 * @param None
 * @return void
*/
void where_to_go(){
     int i = 0;
     int lowest_reading = sensor_values_processed[0];
     int index = 0;

	 /* Check the front reading for potential reverse driving */
    if(front_reading[0] >= 400 || front_reading[1] >= 400 || front_reading[2] >= 400)
    {
        drive_reverse();
        Delay_ms(350);
        stop();
     }

	 /* Find the lowest values in sensor readings for each direction */
     for(i = 0; i < DIRECTIONS; i++)
     {
         if(sensor_values_processed[i] < lowest_reading)
         {
             lowest_reading = sensor_values_processed[i];
             index = i;
         }
     }

     /* Determine the directions to go */
     switch(index)
     {
         case 0:
           drive_full_left();
           break;
         case 1:
           drive_small_left();
           break;
         case 2:
           drive_forward();
           break;
         case 3:
           drive_small_right();
           break;
         case 4:
           drive_full_right();
           break;
         default:
           stop();
           break;
     }

}


/**
 * @brief Main function of the program, entry point.
 *
 * This function is an entry point of the program. It does all neccesary configuration of all
 * the modules of the program (MCU, servo_sensor, car_drive etc.)
 * In the infinite while loop program is continously driving the vehicle, stops at obstacles
 * scans the space when needed etc.
*/
void main()
{
    
        unsigned i = 0;

        AD1PCFG = 0xFDFF;        // set all pins to digital except pin AN9(RB15)
        LATB = 0;
        TRISB = 0;
        TRISB.F15 = 1;          // set pin AN9(RB15) as input

		/* Initialization of needed components */
        initialize_car_drive();
        Delay_ms(100);
        initialize_servo_sensor();
        Delay_ms(100);
        set_servo_sensor_to_starting_pos();
        Delay_ms(300);

		/* At the start vehicle just drives forward */
        drive_forward();
        while(1)
        {
        		/* Drive forward until obstacle, get sensor reading and decide where to go */
                sensor_reading = ADC1_Get_Sample(9);
                if(sensor_reading >= 300)
                {
                        stop();
                        scan_space_with_sensor();
                        where_to_go();
                 }
        }
}

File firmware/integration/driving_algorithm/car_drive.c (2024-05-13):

/**
 * @file car_drive.c
 * @brief File containing function definitons for vehicle moving.
 * This file contains several function definition that are needed
 * for driving the the vehicle. There are 5 possible directions of
 * moving: forward, left, full left, right, full right. Alse there is
 * additional directions that is used in some cases: reverse.
 * Since I2C interface is needed for driving the vehicle, there is alse
 * initialization of I2C interface, and function for sending I2C messages.
*/

#include "car_drive.h"

/**
 * @name Macros used in program 
 * @{
*/
/** @brief Macro that defines speed of the vehicle (0-255) */ 
#define SPEED 125
/** @brief I2C address of the device */
#define DEVICE_ADDR 0xE0
/** @} */

/**
 * @name I2C Communication
 * Enable Software I2C communication, through the desired pins
 * @{
*/
sbit Soft_I2C_Sda           at RB2_bit;
sbit Soft_I2C_Scl           at RB3_bit;
sbit Soft_I2C_Sda_Direction at TRISB2_bit;
sbit Soft_I2C_Scl_Direction at TRISB3_bit;
/** @} */


/*
 * Function for I2C controller configuration. It start I2C communication, 
 * addresses device, then desired register, and puts some value appropriate value in it.
 * At the end it stops the communication.
*/
void static I2C_Send_Message(unsigned short dev_addr, unsigned short reg_addr, unsigned short data_value)
{
    Soft_I2C_Start();
    Soft_I2C_Write(dev_addr);
    Soft_I2C_Write(reg_addr);
    Soft_I2C_Write(data_value);
    Soft_I2C_Stop();
}


/*
 * Function that initializes I2C communication. It inits I2C, then sets MODE1 register of
 * PCA9633 device with appropriate bit setting (AIx to 000, SLEEP to 0, SUBx to 000, ALLCALL to 1).
 * After that set LEDOUT register to 0xAA
*/
void initialize_car_drive(){
    Soft_I2C_Init();
    Delay_ms(100);
    I2C_Send_Message(DEVICE_ADDR, 0x00, 0x01);
    I2C_Send_Message(DEVICE_ADDR, 0xE8, 0xAA);
}

/*
 * Function for setting PWMx registers of PCA9633 to appropriate
 * values for going forward.
*/
void static forward()
{
    I2C_Send_Message(DEVICE_ADDR, 0x02, 0);
    I2C_Send_Message(DEVICE_ADDR, 0x03, SPEED);
    I2C_Send_Message(DEVICE_ADDR, 0x04, 0);
    I2C_Send_Message(DEVICE_ADDR, 0x05, SPEED);
}


/*
 * Function for setting PWMx registers of PCA9633 to appropriate
 * values for driving backwards.
*/
void static reverse()
{
    I2C_Send_Message(DEVICE_ADDR, 0x02, SPEED);
    I2C_Send_Message(DEVICE_ADDR, 0x03, 0);
    I2C_Send_Message(DEVICE_ADDR, 0x04, SPEED);
    I2C_Send_Message(DEVICE_ADDR, 0x05, 0);
}

/*
 * Function for setting PWMx registers of PCA9633 to appropriate
 * values for braking.
*/
void static brake()
{
    I2C_Send_Message(DEVICE_ADDR, 0x02, 0);
    I2C_Send_Message(DEVICE_ADDR, 0x03, 0);
    I2C_Send_Message(DEVICE_ADDR, 0x04, 0);
    I2C_Send_Message(DEVICE_ADDR, 0x05, 0);
}


/*
 * Function for setting PWMx registers of PCA9633 to appropriate
 * values for going left.
*/
void static left()
{
    I2C_Send_Message(DEVICE_ADDR, 0x02, 0);
    I2C_Send_Message(DEVICE_ADDR, 0x03, 0);
    I2C_Send_Message(DEVICE_ADDR, 0x04, 0);
    I2C_Send_Message(DEVICE_ADDR, 0x05, SPEED);

}


/*
 * Function for driving vehicle right. Setting PWMx registers of PCA9633 to appropriate
 * values for going right.
*/
void static right()
{
    I2C_Send_Message(DEVICE_ADDR, 0x02, 0);
    I2C_Send_Message(DEVICE_ADDR, 0x03, SPEED);
    I2C_Send_Message(DEVICE_ADDR, 0x04, 0);
    I2C_Send_Message(DEVICE_ADDR, 0x05, 0);

}


/*
 * Function for driving vehicle forward. This is just basically going forward.
*/
void drive_forward()
{
    forward();
}


/*
 * Function for driving vehicle backwards. This is just basically going reverse.
*/
void drive_reverse(){
    reverse();
}


/*
 * Function for stopping the vehicle.
*/
void stop()
{
    brake();
}

/*
 * Function for driving the vehicle 90 degrees to the left. This means driving
 * vehicle left for some time, needed for it to turn left 90 degrees, and then 
 * driving forward.
*/
void drive_full_left(){
    // go left 90 degress
    left();
    Delay_ms(1100);
    brake();

     // go forward
    drive_forward();

}



/*
 * Function for driving the vehicle 45 degrees to the left. This means driving
 * vehicle left for some time, needed for it to turn left 45 degrees, and then 
 * driving forward.
*/
void drive_small_left(){
    // go left 45 degress
    left();
    Delay_ms(850);
    brake();

    // go forward
    drive_forward();

}


/*
 * Function for driving the vehicle 90 degrees to the left. This means driving
 * vehicle left for some time, needed for it to turn left 90 degrees, and then 
 * driving forward.
*/
void drive_full_right(){
    right();
    Delay_ms(1100);
    brake();

    // go forward
    drive_forward();
}



/*
 * Function for driving the vehicle 90 degrees to the left. This means driving
 * vehicle left for some time, needed for it to turn left 90 degrees, and then 
 * driving forward.
*/
void drive_small_right(){
    right();
    Delay_ms(850);
    brake();

    // go forward
    drive_forward();
}

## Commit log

2024-01-28 -Dodavanje osnovne šeme sa mikrokontrolerom i minimalnom konfiguracijom
    - Dodavanje dokumentacije u vezi dodavanja osnovne šeme
    [SemaV1.kicad_pcb, SemaV1.kicad_sch]
2024-01-30 - Azuriranje seme
    - Dodavanje modula za WiFi
    [SemaV1.kicad_sch]
2024-01-30 -Dodavanje bloka za programiranje na šemu
    - Podrazumijeva dodavanje konektora za pinove i spajanja sa mikrokontrolerom
    [SemaV1.kicad_sch]
2024-01-30 -Dodavanje modela projektovanog edge connector-a
    -Dodavanje simbola i dodavanje footprint-a
2024-01-31 Azuriranje seme
    - Dodavanje edge connector-a na semu, spajanje I2C pinova sa mikrokontrolera i spajanje napajanja i mase
    - Dodavanje ostalih konektora za eksterne interfejse (I2C, UART, SPI)
    [SemaV1.kicad_sch]
2024-01-31 Dodavanje dokumentacije projektovanja šeme, nakon dodavanja dijelo o napajanju, edge connector-u i eksternim interfejsima
2024-01-31 -Dodavanje testnih tacaka na semu, za potrebe kasnijeg testiranja
    - Izmjena imena foldera iz semav1 u sema
    [SemaV1.kicad_pcb, SemaV1.kicad_sch]
2024-02-01 Dodavanje završnog dizajna pločice
    Rutiranje komponenata
    [SemaV1.kicad_pcb, SemaV1.kicad_sch]
2024-02-07 Dodavanje pcb fajla sa rutiranim komponentama
    Sitne izmjene sa semi
    [SemaV1.kicad_pcb, SemaV1.kicad_sch]
2024-02-07 Dodavanja .csv fajla sa odabirom komponenata
    [komponente.csv]
2024-02-25 Issue #25: Izmjena fajl hijerarhije na repozitorijum i sredjivanje dokumentacije
    - Dodavanje docs podfoldera za smjestanje dokumenteacije i izvjestaja
    - Sredjivanje podfoldera pcb_design. Izmjenjen naziv foldera sema u kicad_schematic_pcb jer se unutra nalaze kicad fajlovi projekta
    - Dodavanje .gitignore fajla sa ignorisanje nepotrebnih kicad fajlova
    [control_board.kicad_pcb, control_board.kicad_sch, komponente.csv]
2024-02-26 Issue #22 : Rutiranje PCB-a
    - Izmjene footprint-a svih otpornika
    - Izmjene rutiranja komponenata u skladu sa primjedbama
    [control_board.kicad_pcb, control_board.kicad_sch]
2024-02-26 Issue #25: Izmjena fajl hijerarhije na repozitorijum i sredjivanje dokumentacije
    - Izmjena layout_3d_model.pdf fajla zbog izmjena u rutiranju pcb-a
2024-03-30 Issue #36: Testiranje stampane plocice nakon lemljenja komponenata
    -Testiranje spustanja programa na mikrokontroler
    -Dodavanje C programa za mikroC kompajler kojim se na pinu RB15 pali i gasi led dioda svake sekunde
    [led_blinking.c]
2024-03-30 Issue #34: Simuliranje mapiranja prostora oko vozila
    -Python aplikacija koja simulira mapiranje prostora oko senzora koristeci pygame modul iz python-a
    -Dodavanje fajla sensor.py, koji u sebi sadrzi klasu Sensor i u kojoj se simulira rad senzora
    -Dodavanje fajla main.py koji u sebi sadrzi glavni program i ukljucuje senzor te iscrtava prostor oko njega
    [led_blinking.c]
2024-03-30 Issue #38: Testiranje IR Distance Click komponente
    -Dodavanje C fajla za mikroC kompajler
    -Program konfigurise jedan port mikrokontrolera kao analogni ulazni pin na koji se dovodi izlaz senzora
    -Konfigurise AD konvertor za konverziju podataka sa analognog pina
    -Na osnovu vrijednosti sa senzora i postavljenog praga, odlucuje da li se ukljucuje ili iskljucuje dioda povezana na jedan izlazni digitalni pin
    [sensor.c]
2024-04-08 Issue #42 : Testiranje i pokretanje servo motora za senzor
    [servo.c]
2024-04-15 Issue #43: Konfiguracija I2C-a za pokretanje motora na tockovima
    - Dodavanje koda za testiranje pokretanja motora tockova na vozilu
    - Dodan je testni C kod za mikroC kompajler koji konfigurise vozilo tako da se krece naprijed
    [wheels.c]
2024-04-18 Issue #44: Konfiguracija WiFi modula
    - Dodavanje C fajla za testiranje WiFi modula
    [wifi_test.c]
2024-04-24 Issue #48: Integrisanje rada servo motora i rada senzora Dodan C fajl
    [servo_sensor.c]
2024-04-25 Issue #46: Kreiranje algoritma kretanja vozila na osnovu očitavanja senzora - Dodavanje testnog .c programa u kojem se integrise rad senzora i servo motora sa točkovima
    [drive_servo_sensor.c]
2024-05-08 Issue #44: Konfiguracija WiFi modula
    -Dodavanje izmjenjenog koda za testiranje rada wifi modula
    -Izmjena se odnosi na koristenje UART interapta umjesto poling principa
    -Druga izmjena je brisanje flega koji kada je setovan oznacava da je UART fifo bafer pun, svaki put kada se desi UART Error interapt
    [wifi_test.c]
2024-05-09 Issue #46: Kreiranje algoritma kretanja vozila na osnovu ocitavajna senzora
    - Razdvajanje programa na module radi bolje citljivosti
    - Program podijeljen u modul koji se odnosi na sensor: servo_sensor.c(.h) i koji se odnosi na upravljanje vozilom car_drive.c(.h)
    - Dodavanje Doxygen komentara radi generisanja dokumentacije
    [car_drive.c, main_program.c, servo_sensor.c]
2024-05-10 Issue #46: Kreiranje algoritma kretanja vozila na osnovu ocitavajna senzora
    - Unaprijedjenje algoritma kretanja
    - Mogucnost kretanja unazad kada se vozilo nadje u situaciji kada ne moze da ide ni u jednom od mogucih pet pravaca
    - Bolje skeniranje prostora nakon zaustavljanja
    - Dodavanje koementara za Doxygen dokumentaciju
    [car_drive.c, modular_drive_car.c, servo_sensor.c]
2024-05-10 Issue #46: Kreiranje algoritma kretanja vozila na osnovu ocitavajna senzora
    - Uklanjanje starog nepotrebnog main_program.c fajla
    [main_program.c]
2024-05-13 Issue #47: Sredjivanje wiki dokumentacije i dokumentacija koda
    - Sredjivanje, dodavanje i ispravljanje komentara u kodu
    - Promjena imena fajla sa main funckijom iz modular_drive_car.c u main_program.c
    [car_drive.c, main_program.c, servo_sensor.c]
2024-05-14 Issue #47: Sredjivanje wiki dokumentacije i dokumentacija koda
    - Dodavanje Doxygen dokumentacija za /integration/servo_sensor.c fajl, kao i dodavanje index.html fajla za generisanom dokumentacijom
    [servo_sensor.c]
2024-05-14 Issue #47: Sredjivanje wiki dokumentacije i dokumentacija koda
    - Dodavanje Doxygen dokumentacija za /integration/drive_servo_sensor.c fajl, kao i dodavanje index.html sa generisanom dokumentacijom
    [drive_servo_sensor.c]
2024-05-14 Issue #47: Sredjivanje wiki dokumentacije i dokumentacija koda
    - Dodavanje dokumentacije za testing/ir_distance_click
    [sensor.c]
2024-05-14 Issue #47: Sredjivanje wiki dokumentacije i dokumentacija koda
    - Dodavanje doxygen generisane dokumentacije za testing/led_blinking
    [led_blinking.c]
2024-05-14 Issue #47: Sredjivanje wiki dokumentacije i dokumentacija koda
    - Dodavanje doxygen generisane dokumentacije za testing/servo_sensor
    [servo.c]
2024-05-14 Issue #47: Sredjivanje wiki dokumentacije i dokumentacija koda
    - Dodavanje doxygen generisane dokumentacije za testing/wheels_i2c
    [wheels.c]
